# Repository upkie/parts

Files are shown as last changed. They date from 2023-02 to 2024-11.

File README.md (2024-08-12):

# 3D printed parts for Upkie

This repository provides [3D printing](https://github.com/upkie/upkie_parts/tree/main/3d_printing) (3MF and STL files), [CAD files](https://github.com/upkie/upkie_parts/tree/main/cad) (Blender, FreeCAD) and Markdown files to keep track of part history.

> [!NOTE]\
> We maintain parts in this separate repository because their full revision history is quite memory-consuming. Only part designers should have to clone this repository; most users will only clone the main [upkie](https://github.com/upkie/upkie) repository.

## Assembly

Assembly files are also available on Hackaday.io:

- [`upkie.blend`](https://cdn.hackaday.io/files/1857297946229536/upkie-blender.zip): Blender project of the fully assembled robot
- [`upkie.stl`](https://cdn.hackaday.io/files/1857297946229536/upkie-stl.zip): STL model of the fully assembled robot

## Add-ons

### Earflap

Provisional connector to attach a [60x60x25 mm, 24 V DC fan](https://www.amazon.fr/Ventilateur-60x60x25mm-22dBA-Sunon-MF60252V21000UA99/dp/B07ZBSBP33/) to Upkie's head. Helps avoid thermal throttling when the robot actively balances for more than one hour.

* [STL file](add-ons/earflap/earflap.stl)

### Handle

Regular handle to grab the robot and move it around.

* [STL file](add-ons/handle/handle.stl)
* [Blender project](add-ons/handle/handle.blend)



### Switch support

A small part to hold the on-off switch, and have it easy to access on the side of the robot.

* [STL file](add-ons/switch_support/switch_support.stl)
* [FreeCAD file](add-ons/switch_support/switch_support.FCStd)

## See also

- [Build instructions](https://github.com/upkie/upkie/wiki): printing and assembling a new Upkie
- [Discussions](https://github.com/upkie/upkie/discussions): around Upkie's hardware and software
- [mjbots/quad](https://github.com/mjbots/quad/tree/main/hw/chassis/3dprint): an open-source quadruped from which torso meshes in Upkie were initially imported

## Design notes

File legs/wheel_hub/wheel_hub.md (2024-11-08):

Wheel Hub
===

## Revisions

### 2024/11/07
- Made the wheel and wheel hub a single piece. Added an outer lip to keep the tire in place.

### 2023/04/11
- Add a flange at the base of the shaft, to distribute torsion effort from the flat part of the screw to the 'cone' via the flange. (and don't rely only on the 'fragile' shaft).
- Add a chamfer to tip the of the shaft, to prevent it from deforming and locking the nut when pushing the hub out of the wheel.
- Shorten the shaft, so the user pushes on the nut (instead of the shaft) to get the hub out of the wheel.
- Include a tool to increase the resistance of the shaft when holding it in a drill. (Useful if the outside diameter of the hub needs to be decreased)

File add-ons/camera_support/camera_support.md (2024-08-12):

# Camera support

Support for an OAK-D Lite camera.

## Revisions

### 2024-08-12

- Correct top-face hole diameters to 4.85 mm (rather than 5 mm)

### 2023-04-18

- Enlarge USB cable gutter to 15 mm (rather than 10 mm)
- Redefine top holes as M3x5x4 insert holes (rather than screw holes)

### 2023-03-30

- Add pocket for USB-C cable

### 2023-02-20

Initial version.

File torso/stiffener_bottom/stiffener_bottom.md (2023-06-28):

# Stiffener (bottom)

## Revisions

### 2023/06/15

- Translate all four corners 4 mm towards their respective hex socket holes

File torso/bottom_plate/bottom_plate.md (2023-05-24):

# Hollow ankle

## Revisions

### 2023/05/23

- Add "XT90" text on the XT90-S connector side to help identify it
- Increase cylinder base diameter from 7.9 mm to 15.8 mm (same as head plate)
- Increase cylinder height from 6.3 mm to 9 mm (same as head plate)
- Translate cylinder top faces 1.3 mm up

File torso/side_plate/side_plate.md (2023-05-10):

# Side plate

## Revisions

### 2023/05/10

- Bring cable guide 1 cm closer to the fan opening
- Center cable guide

### 2023/05/05

- Fill unused middle wide opening
- Replace switch opening by a circular cable guide
- Switch top opening from qdd100 beta 2 to 60x60x15 fan

### 2023/05/04

- Translated back lower corner coordinates by Y+5 mm
- Switch qdd100 back pattern to beta 3 format (circular)

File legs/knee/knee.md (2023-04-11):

# Hollow knee

## Revisions

### 2023/03/16

- Enlarge M3 screw head hole diameters by +0.3 mm
- We print vertically now, so the holes are tighter than before.

### 2023/03/08

- Adapt back shape to qdd100 beta 3

### 2022/05/22

- Fix the missing top screws!
- Flatten the bone-knee contact surface
- Flatten bottom as well

### 2022/05/21

- Widen hex hole to 28 + 0.6 mm ($0.3 \sqrt{3}/2$ mm tolerance / edge)
- Because we don't want to hammer parts in while connected to the actuator.
- Note the $\sqrt{3}/2$ factor to convert from diameter to edge tolerance!

### 2022/05/07

- Switch to M3x8 screws: 3 mm in part, 5 mm in heat-set insert
- Increase hex dimensions from 28 + 0.2 mm to 28 + 0.3 mm
- Hollow hex part is exactly 60 mm to match the bone
- ... followed by a 28 + 0.3 mm full cylinder for positioning (removes the excess material that prevented full insertion of the hex in v5)

### 2022/05/04

- Use M4x10 screws: 4 mm in part + 6 mm inside heat-set insert

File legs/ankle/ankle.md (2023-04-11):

# Hollow ankle

## Revisions

### 2023/03/29

- Add a 5 mm bevel to the ground side
- Switch from cylinder to hex bone shape
- Switch bone screws to M3

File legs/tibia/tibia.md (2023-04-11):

# Hollow tibia

## Revisions

### 2023/03/31

- Adapt from hollow femur, swap screw holes to the same side

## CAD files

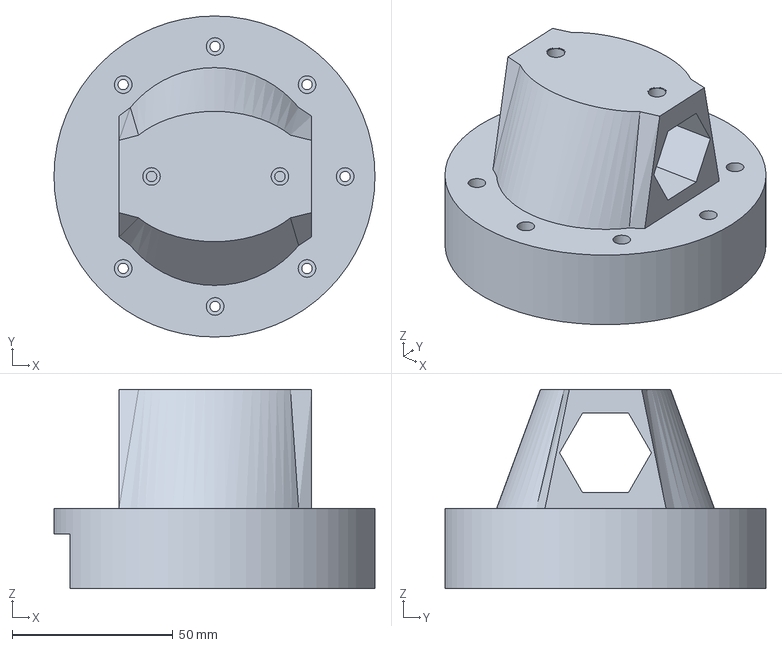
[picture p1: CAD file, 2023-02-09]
3d_printing/extras/knee_qdd100_beta_2.3mf
100.0 x 100.0 x 62.0 mm

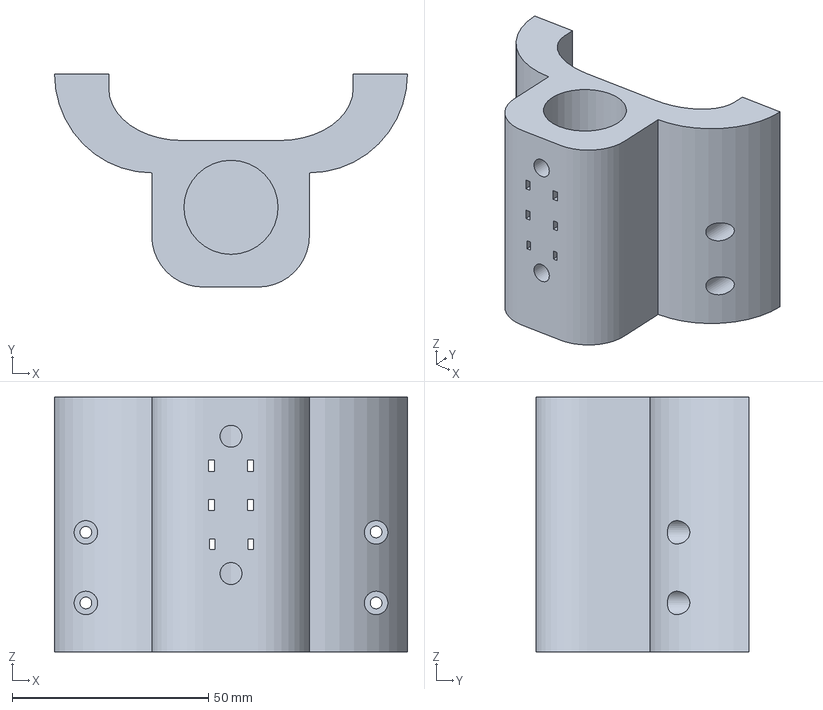
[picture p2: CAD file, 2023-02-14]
3d_printing/extras/wooden_legs/wooden_ankle_v5.3mf
90.0 x 54.3 x 65.0 mm

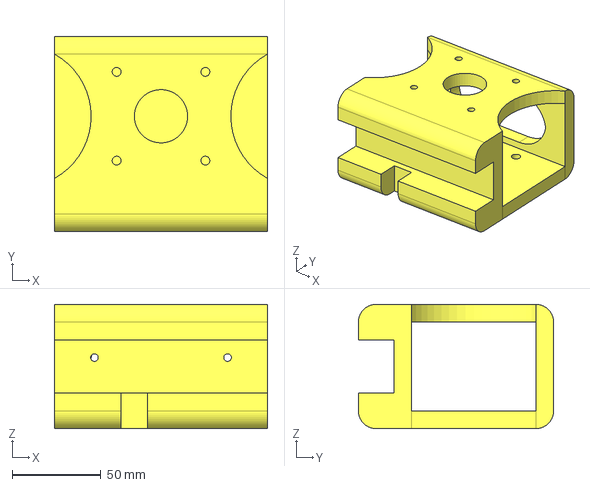
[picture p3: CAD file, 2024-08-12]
add-ons/camera_support/camera_support.FCStd
120.0 x 110.0 x 70.0 mm

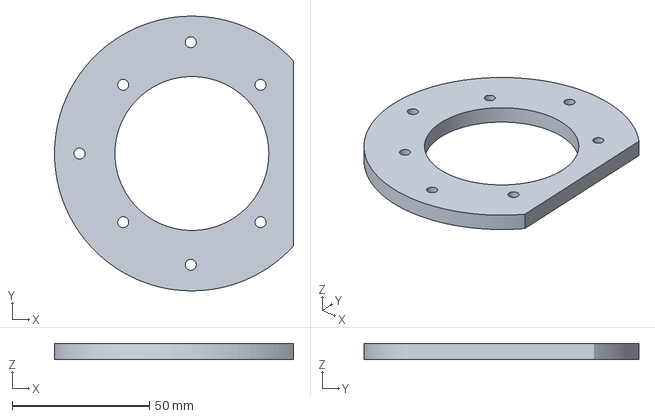
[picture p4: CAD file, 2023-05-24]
add-ons/earflap/earflap.3mf
87.0 x 100.0 x 6.00 mm

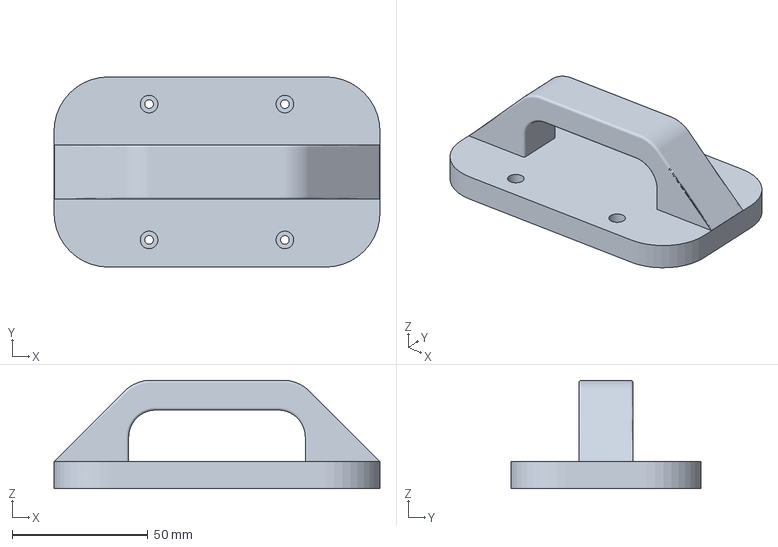
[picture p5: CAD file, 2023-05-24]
add-ons/handle/handle.3mf
120.0 x 70.0 x 39.9 mm

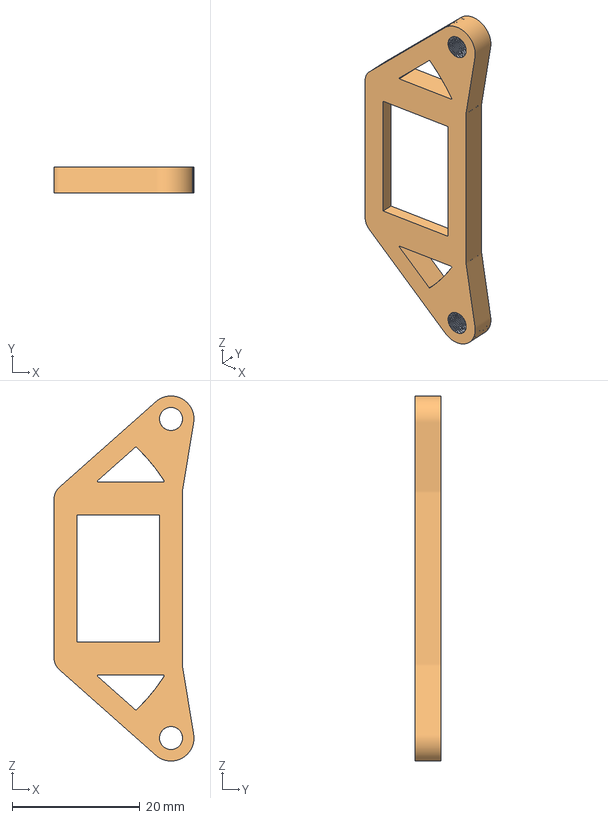
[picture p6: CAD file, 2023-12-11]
add-ons/switch_support/switch_support.FCStd
21.9 x 4.00 x 57.2 mm
Switch_Support
Switch_Support (Meshed)

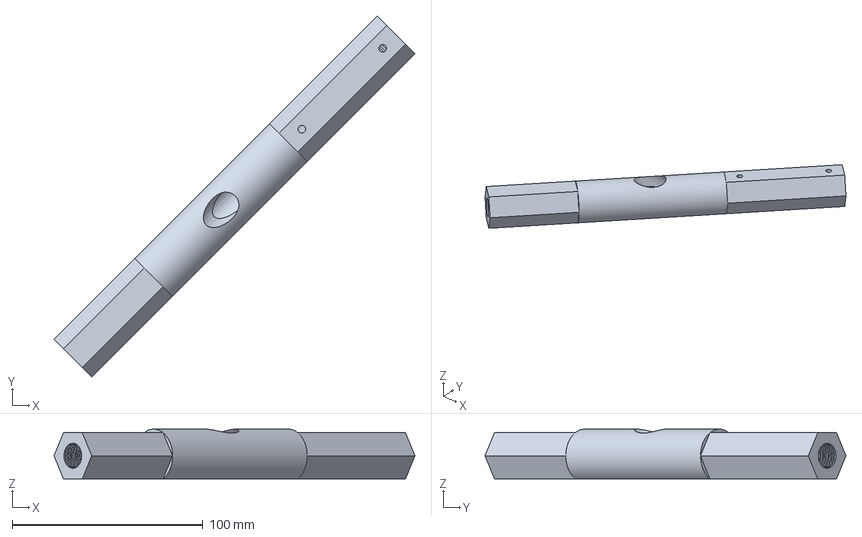
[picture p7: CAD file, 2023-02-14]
legs/femur/femur.3mf
189.5 x 189.5 x 26.1 mm

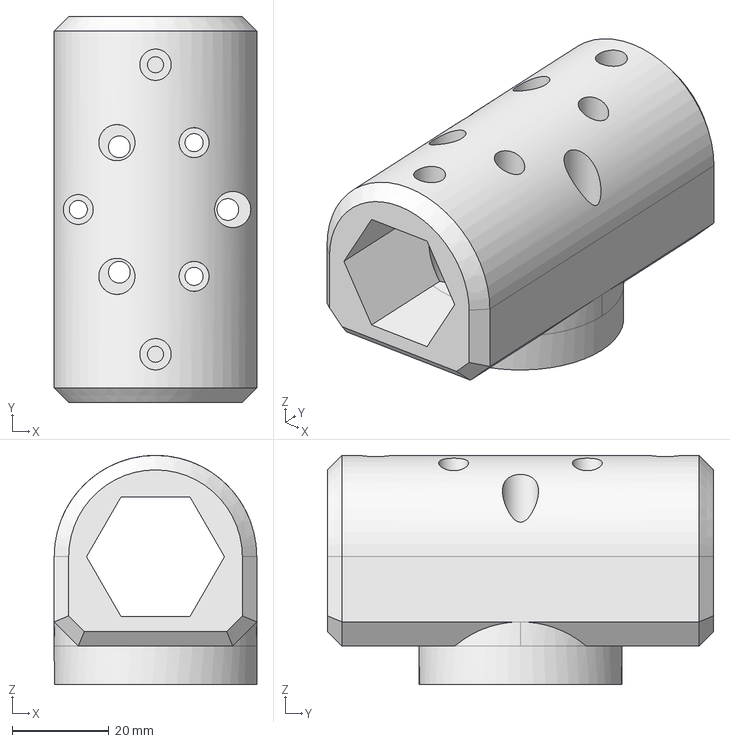
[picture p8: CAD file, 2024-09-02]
legs/horn/horn.FCStd
42.0 x 80.0 x 47.5 mm

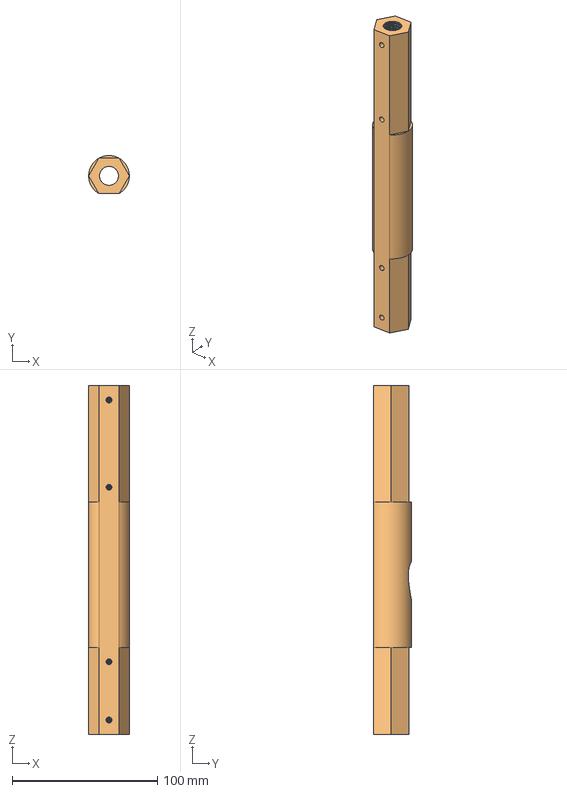
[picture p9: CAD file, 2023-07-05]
legs/tibia/tibia.FCStd
28.0 x 26.1 x 240.0 mm
Cylinder006 (Meshed)

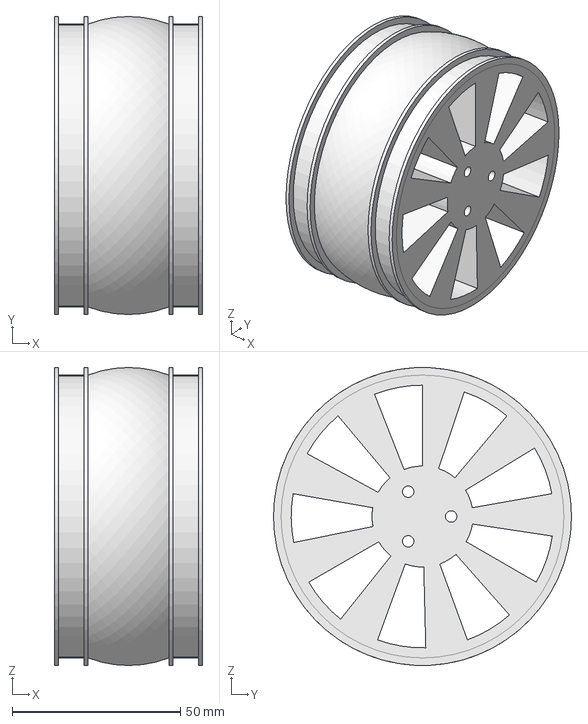
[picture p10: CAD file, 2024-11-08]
legs/wheel_hub/wheel_hub.FCStd
44.0 x 88.5 x 88.5 mm

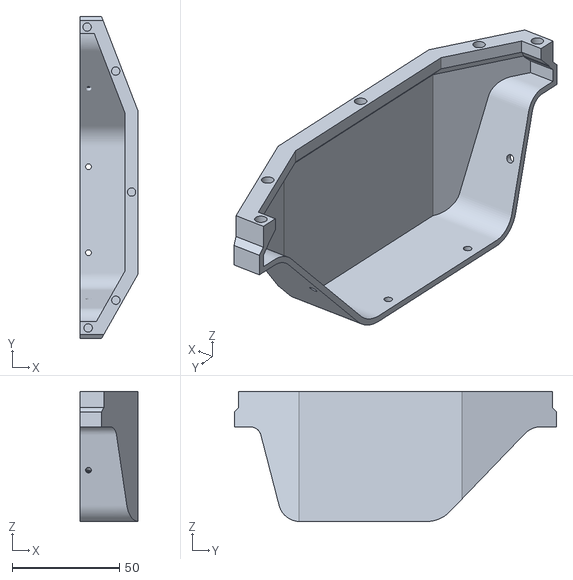
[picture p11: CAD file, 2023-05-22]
torso/back_covers/back_cover_bottom.stl
27.0 x 150.0 x 60.5

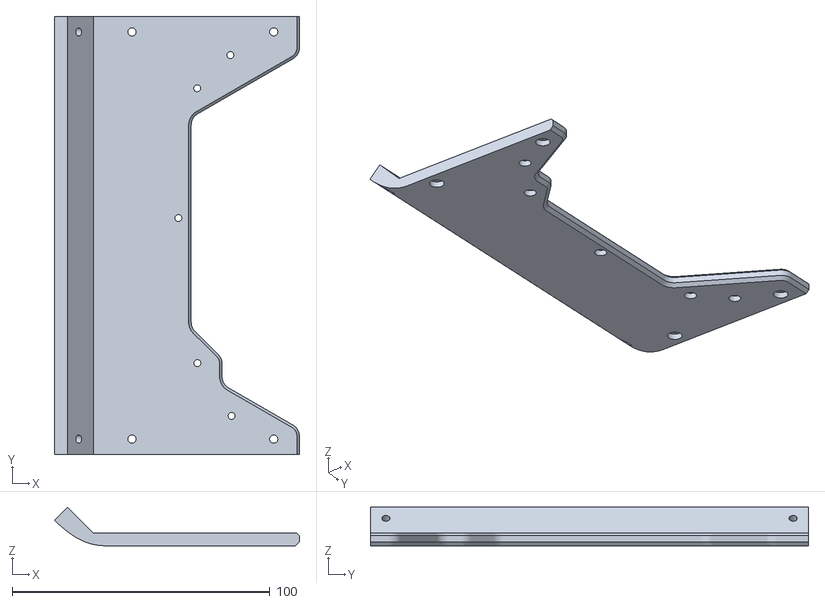
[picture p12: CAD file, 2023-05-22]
torso/back_plates/back_plate_top.stl
95.1 x 170.0 x 15.0

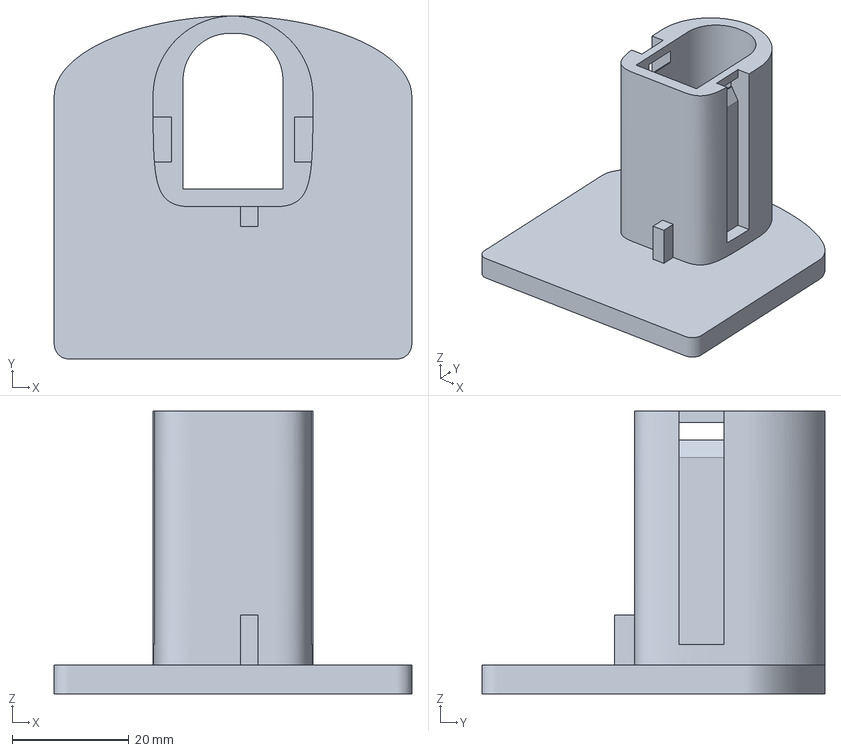
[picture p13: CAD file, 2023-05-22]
torso/battery_shore_plug/battery_shore_plug.3mf
61.3 x 58.8 x 48.5 mm

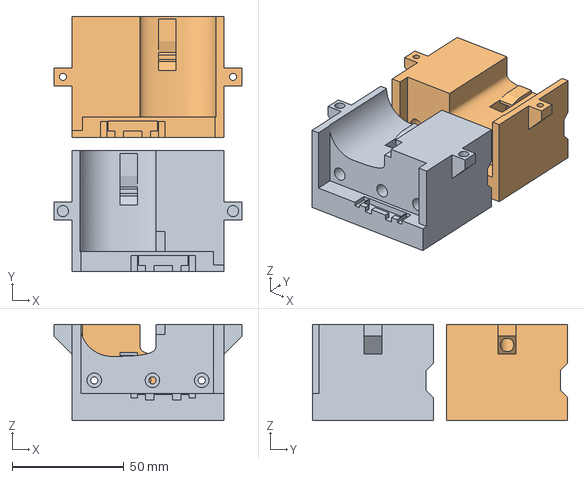
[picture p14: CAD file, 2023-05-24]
torso/battery_stud/battery_stud.3mf
84.0 x 114.0 x 43.0 mm
battery_stud_bottom.stl
battery_stud_top.stl

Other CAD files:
legs/ankle/ankle.FCStd
legs/knee/knee.3mf
torso/bottom_plate/bottom_plate.3mf
torso/face_plate/face_plate.3mf
3d_printing/extras/wooden_legs/wooden_horn_v1.3mf
3d_printing/extras/wooden_legs/wooden_knee_v1.3mf
add-ons/camera_support/camera_support.3mf
add-ons/camera_support/camera_support.blend
add-ons/camera_support/camera_support.stl
add-ons/earflap/earflap.stl
add-ons/handle/handle.blend
add-ons/handle/handle.stl
add-ons/switch_support/switch_support.stl
legacy/wooden_horn_v1.3mf
legacy/wooden_knee_v1.3mf
legs/ankle/ankle.3mf
legs/ankle/ankle.blend
legs/ankle/ankle.stl
legs/femur/femur.blend
legs/femur/femur.stl
legs/horn/horn.stl
legs/knee/knee.blend
legs/knee/knee.stl
legs/tibia/tibia.3mf
legs/tibia/tibia.blend
legs/tibia/tibia.stl
legs/wheel_hub/wheel_hub.stl
torso/back_covers/back_cover_top.stl
torso/back_covers/back_covers.3mf
torso/back_plates/back_plate_bottom.stl
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

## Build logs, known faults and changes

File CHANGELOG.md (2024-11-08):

# Changelog

All notable changes to this project will be documented in this file.

The format is based on [Keep a Changelog](https://keepachangelog.com/en/1.0.0/),
and this project adheres to [Semantic Versioning](https://semver.org/spec/v2.0.0.html).

## [Unreleased]

### Changed

- Redesign the wheel hub (thanks to @Tordjx and @EtienneAr)
## [1.1.0] - 2024-09-02

### Added

- CAD: Camera support
- CAD: Horn in FreeCAD
- CAD: Switch support

### Changed

- Add M4 holes to the horn
- Reorganize directories by part

## [1.0.0] - 2023-07-07

### Added

- CAD: Ankle in FreeCAD (thanks to @christophebraillon)
- CAD: Bottom plate
- CAD: Tibia in FreeCAD (thanks to @standesalpes)
- STL files for all parts, along with 3MF project files

### Changed

- Bottom plate upgrade
- Hollow legs become the default

### Fixed

- Name of stiffener and back cover files relative to top and bottom

## [0.1.0] - 2023-05-12

### Added

- 3D printed part: Back covers
- 3D printed part: Back plates
- 3D printed part: Battery shore plug
- 3D printed part: Battery stud
- 3D printed part: Bottom plate
- 3D printed part: Earflap
- 3D printed part: Face plate
- 3D printed part: Handle
- 3D printed part: Head plate
- 3D printed part: Hollow ankle
- 3D printed part: Hollow femur
- 3D printed part: Hollow horn
- 3D printed part: Hollow knee
- 3D printed part: Hollow knee for qdd100 beta 2
- 3D printed part: Hollow tibia
- 3D printed part: Side plate
- 3D printed part: Stiffener bottom
- 3D printed part: Stiffener top
- 3D printed part: Wheel hub
- 3D printed part: Wooden ankle
- 3D printed part: Wooden horn
- 3D printed part: Wooden knee
- CAD: Handle
- CAD: Head plate
- CAD: Hollow ankle
- CAD: Hollow femur
- CAD: Hollow horn
- CAD: Hollow knee
- CAD: Hollow tibia
- CAD: Side plate
- CAD: Wheel hub (thanks to @EtienneAr)
- System: CPU isolation
- System: Disable network time synchronization
- System: Install packages
- System: Keyboard configuration
- System: Wireless access point configuration

[unreleased]: https://github.com/upkie/parts/compare/v1.1.0...HEAD
[1.1.0]: https://github.com/upkie/parts/compare/v1.0.0...v1.1.0
[1.0.0]: https://github.com/upkie/parts/compare/v0.1.0...v1.0.0
[0.1.0]: https://github.com/upkie/parts/releases/tag/v0.1.0

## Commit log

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2023-02-08 Revert "[minor] Commercial name is as power_dist"
    This reverts commit e786b04d755ad301d9cafbfaa55a21bc5807eb55.
2023-02-08 Add face plate project file
    [face_plate_v1.3mf]
2023-02-09 Save wooden knee 3MF project
    [wooden_knee_v1.3mf]
2023-02-09 Add hollow knee 3MF project
    [hollow_knee_should_totally_be_printed_it_this_way.3mf, hollow_knee_v1.3mf]
2023-02-09 Start extras/ folder and add earflap project to it
    [earflap_v1.3mf]
2023-02-09 Add handle to extras
    [handle_v1.3mf]
2023-02-09 Mais ce sera pour une prochaine fois ;)
    [hollow_knee_should_totally_be_printed_it_this_way.3mf]
2023-02-09 Add hollow leg 3MF projects
    [hollow_femur_v1.3mf, hollow_hip_v1.3mf, hollow_horn_v1.3mf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]
2023-02-09 Add wheel hub 3MF project
    [wheel_hub_v6.3mf]
2023-02-09 Add ankle and head plate project files
    [ankle_v1.3mf, head_plate_v1.3mf]
2023-02-09 Hollow hip and horn are the same
    [wooden_ankle_v1.3mf]
2023-02-09 Head plate version is actually 2
    [head_plate_v2.3mf]
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2023-02-09 Remove hollow hip (redundant with horn)
    [hollow_hip_v1.3mf]
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2023-02-09 Import initial project files from mjbots/quad
    License: Apache-2.0
    [20200303-battery_stud.3mf, 20200415-stiffener_left.3mf, 20200415-stiffener_right.3mf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]
2023-02-09 WIP: Rename project files to Upkie's layout
    [20200303-battery_stud.3mf, 20200708-shore_plug.3mf, back_covers_v1.3mf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]
2023-02-09 Remove aligners project file
    [20200502-aligners.3mf]
2023-02-09 Rename all parts to Upkie's layout
    [side_plate_v1.3mf]
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2023-02-09 Add wheel hub to hollow leg
    [wheel_hub_v6.3mf]
2023-02-09 Add horn to wooden leg
    [wooden_horn_v1.3mf]
2023-02-09 Update bottom and side plate projects
    [bottom_plate_v1.3mf, side_plate_v1.3mf]
2023-02-09 Move head plate to chassis
    [head_plate_v2.3mf]
2023-02-13 Update stiffeners
    [stiffener_bottom_v1.3mf, stiffener_top_v1.3mf]
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2023-02-13 Add 3D printing instructions
    [20200303-battery_stud.3mf, 20200708-shore_plug.3mf, back_covers_v1.3mf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]
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2023-02-13 Rename chassis to torso
    Follows the release of v1.1.1 for upkie_description
    [20200303-battery_stud.3mf, 20200708-shore_plug.3mf, back_covers_v1.3mf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]
2023-02-13 Number with vertical rather than horizontal lines :lipstick:
    [hollow_femur_v9.3mf, wooden_ankle_v5.3mf]
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2023-02-14 Update hollow_femur_v9 project file
    [hollow_femur_v9.3mf]
2023-02-14 Update wooden_ankle_v5 project file
    [wooden_ankle_v5.3mf]
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2023-02-15 Set hollow knee version number
    [hollow_knee_v8.3mf]
2023-02-15 Set hollow horn version number
    [hollow_horn_v6.3mf]
2023-02-15 Move wheel_hub_v6 to wheels/
    [wheel_hub_v6.3mf]
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2023-03-08 Hollow Knee v8 is for qdd100 beta 2
    [hollow_knee_v8_for_qdd100_beta_2.3mf]
2023-03-08 Add Hollow Knee v9 for qdd100 beta 3
    [hollow_knee_v9.3mf]
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2023-03-29 Add Hollow Ankle v6
    [hollow_ankle_v6.3mf]
2023-03-30 Fix screw hole position in Hollow Ankle v6
    [hollow_ankle_v6.3mf]
2023-03-30 Align screw plates with plate
    [hollow_ankle_v6.3mf]
2023-03-31 Print hollow knee support on build plate only
    [hollow_knee_v9.3mf]
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2023-04-11 [cad] Add hollow ankle
    [hollow_ankle.blend]
2023-04-11 [cad] Add hollow knee
    [hollow_knee.blend]
2023-04-11 [cad] Add hollow femur
    [hollow_femur.blend]
2023-04-11 [cad] Add hollow horn
    [hollow_horn.blend]
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2023-04-11 Re-modeling of Wheel Hub
    [wheel_hub.FCStd]
2023-04-11 Re-generate 3MF for wheel hub
    [wheel_hub.3mf, wheel_hub_v6.3mf]
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2023-04-12 [system] Fix maximum wheel velocity
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2023-04-14 [cad] Add head plate
    [head_plate.blend]
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2023-05-04 Remove version number from torso file names
    [back_covers.3mf, back_plates.3mf, bottom_plate.3mf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]
2023-05-04 Revise side plate for qdd100 beta 3
    [side_plate.blend]
2023-05-04 Slice new side plate model
    [side_plate.3mf]
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2023-05-05 Update side plate 3MF project
    [side_plate.3mf]
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2023-05-10 Revise side plate (bis repetita placent)
    [side_plate.blend]
2023-05-11 Move battery 3MF files together with the others
    [battery_shore_plug.3mf, battery_stud.3mf]
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2023-05-22 Add STL file for face plate
    [face_plate.3mf, face_plate.stl]
2023-05-22 Add STL file for battery shore plug
    [battery_shore_plug.3mf, battery_shore_plug.stl]
2023-05-22 Add STL file for bottom plate
    [bottom_plate.3mf, bottom_plate.stl]
2023-05-22 Add STL file for back cover (bottom)
    [back_cover_bottom.stl]
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2023-05-22 Add STL file for the bottom back plate
    [back_plate_bottom.stl]
2023-05-22 Add STL file for the top back plate
    [back_plate_top.stl]
2023-05-22 Add STL for the battery stud (left part)
    [battery_stud_left.stl]
2023-05-22 Add STL file for the battery stud (right part)
    [battery_stud_right.stl]
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2023-05-22 Add STL files for the stiffeners
    [stiffener_bottom.stl, stiffener_top.stl]
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2023-05-24 Rename battery stud parts to top and bottom
    [battery_stud.3mf, battery_stud_bottom.stl, battery_stud_top.stl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]
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2023-05-25 Make hollow legs the new default
    Move wooden legs to extras/
    [ankle.3mf, ankle.stl, femur.3mf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]
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2023-06-28 Update stiffener_bottom STL
    [stiffener_bottom.stl]
2023-06-28 Update bottom stiffener
    [stiffener_bottom.stl]
2023-07-04 Parametric FreeCAD model of tibia
    R_1 - main radius, R_2 - main hole radius, R_hole - screw hole radius, L_c - length of center part, L_low - length of lower hexa section, L_h - len of higher hexa section
    [tibia.FCStd]
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2024-08-12 camera_support: Correct top-face hole diameters to 4.85 mm
    [camera_support.blend, camera_support.stl]
2024-09-02 Redesign horn in Freecad & add M4 holes
    [horn.3mf, horn.FCStd, horn.blend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]
2024-11-06 Add wheel STL and freecad files, removed wheel hub
    [wheel_hub.3mf, wheel_hub.FCStd, wheel_hub.stl]
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
